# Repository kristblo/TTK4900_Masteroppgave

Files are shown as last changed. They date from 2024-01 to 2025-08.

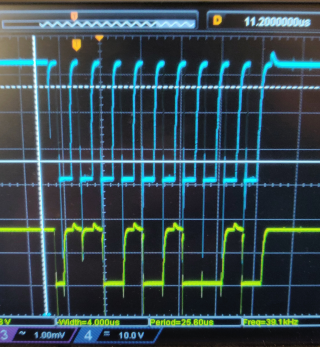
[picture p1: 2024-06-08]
documentation_internal/images/i2c_failure_small.png

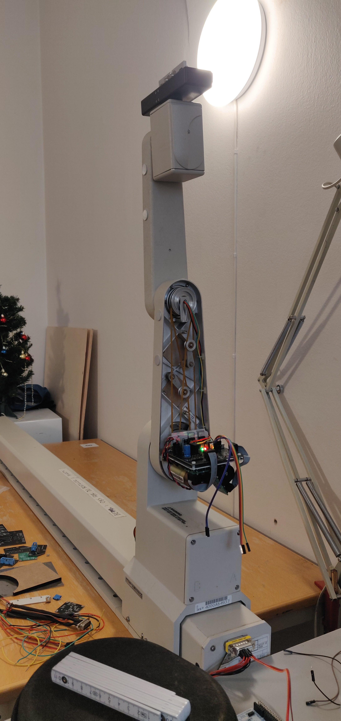
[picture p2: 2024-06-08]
documentation_internal/images/1704_real_arm_calibrated.jpg

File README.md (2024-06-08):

# TTK4900 Masteroppgave

Welcome to the Git repo of the master thesis project of Kristian Blom the spring of 2024, in which a defunct robotic arm from the 1990s was refurbished with new control hardware and software.

The main branch presents the project as it was at the end of the project's implementation, and shall not be altered until final censure has fallen on the project report.

The censure branch presents a curated version of project items deemed relevant to censure. Should the censor(s) find the main branch unnecessarily cluttered, this branch may be of interest.

### Directory: PCBs
Contains KiCad PCB design files.

### Directory: code/ros
Contains all code pertaining to ROS nodes and their configuration.

### Directory: code/stm config official
Contains all code pertaining to arm onboard software modules.

### Directory: documentation external
Contains hardware datasheets, application notes etc. for units used in the project. Most of these are cited as sources in the report.

### Directory: documentation internal
Contains documentation generated for the project.

The file journal.md contains notes taken during development.

A PDF version of the generated code documentation may be found here, in the file "kristian\_blom\_ttk4900\_documentation.pdf".

An HTML version of the generated code documentation may be found here, in the file "kristian\_blom\_ttk4900\_documentation\_html.zip". Its contents may be accessed by downloading and extracting the zip, then accessing "index.html" from a web browser.

Should the configuration of the STM32F303 processor be of interest, beyond what is presented in the thesis, an automatically generated report may be found in "stm\_config\_official.pdf"

Other items in this directory deemed relevant to the censure of the project are presented in the thesis, and may safely be ignored.

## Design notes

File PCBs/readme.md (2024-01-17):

###Folder purpose: PCB designs with Mk1.1 updates implemented, as well as production files such as gerbers

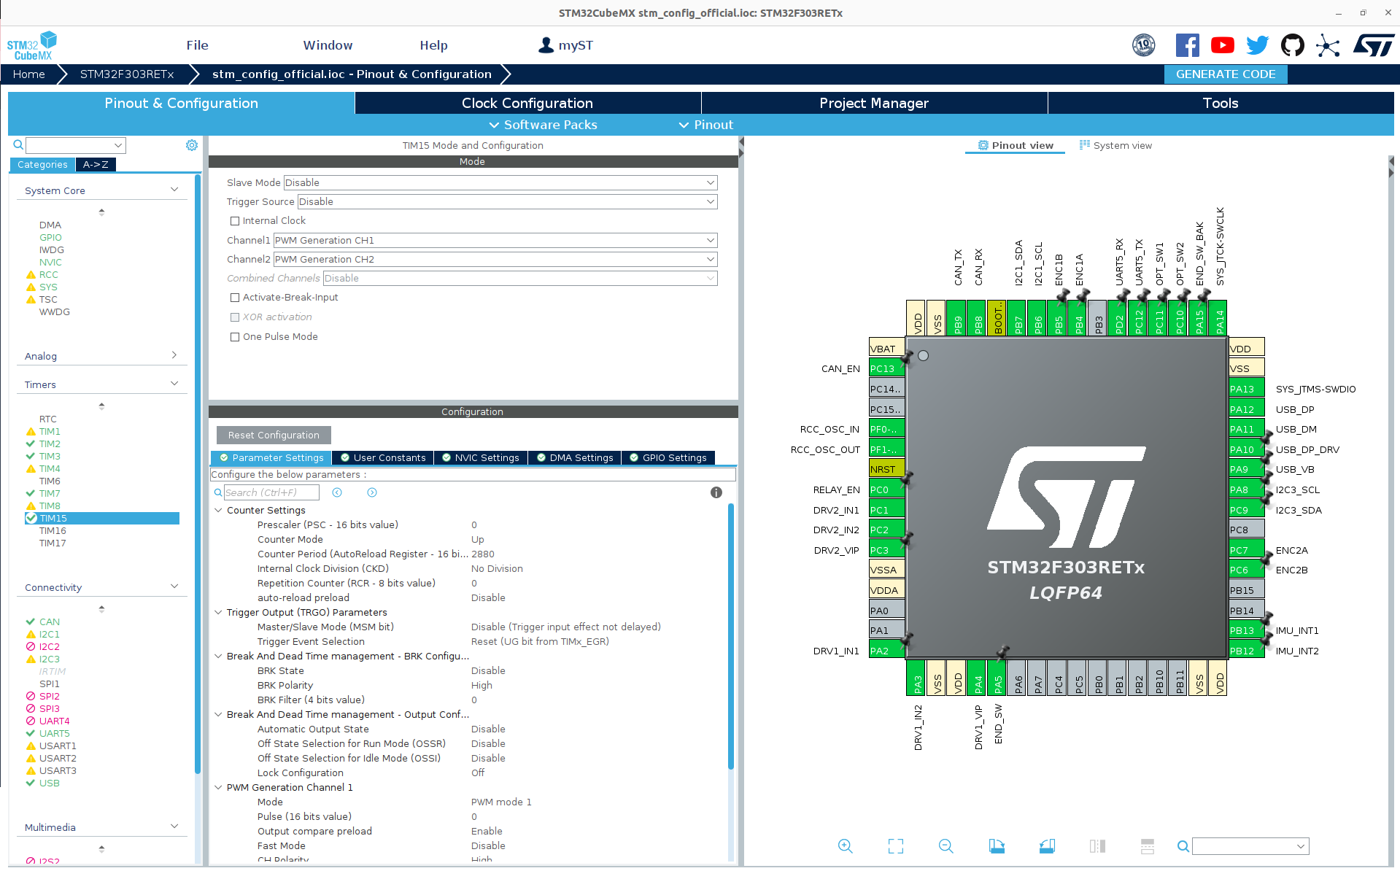
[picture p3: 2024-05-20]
documentation_internal/illustrations/cubemx_pinout_illustration.png

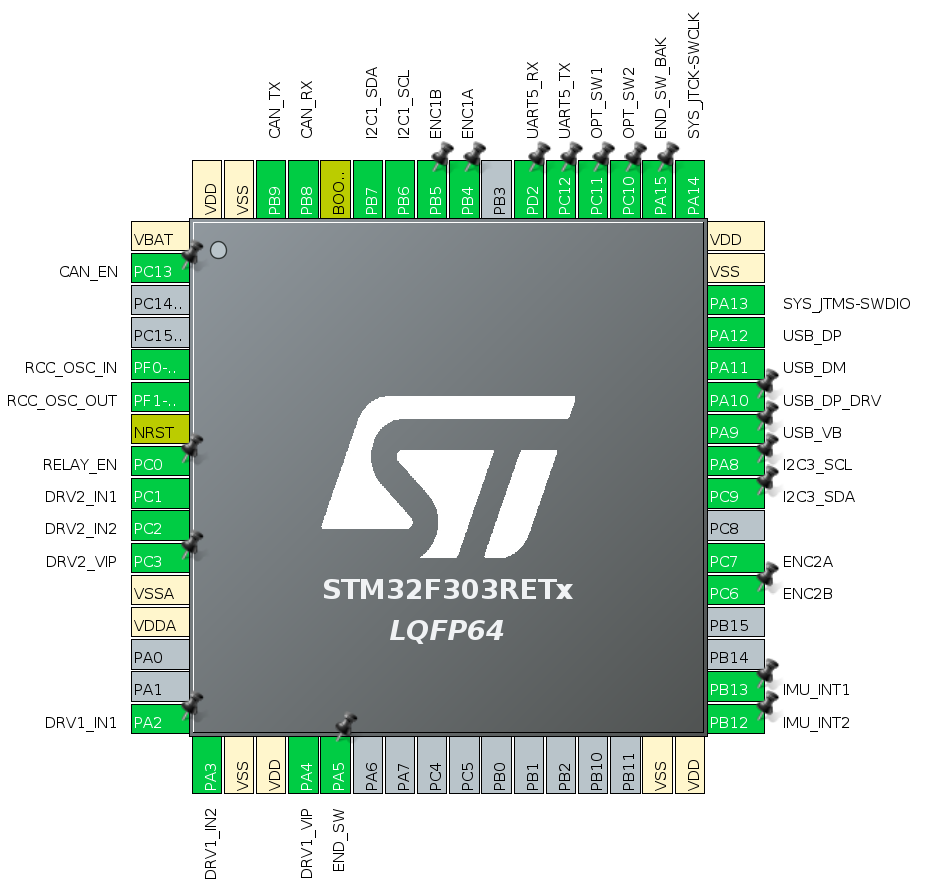
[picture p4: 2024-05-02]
documentation_internal/illustrations/mcu_pinout_illustration.png

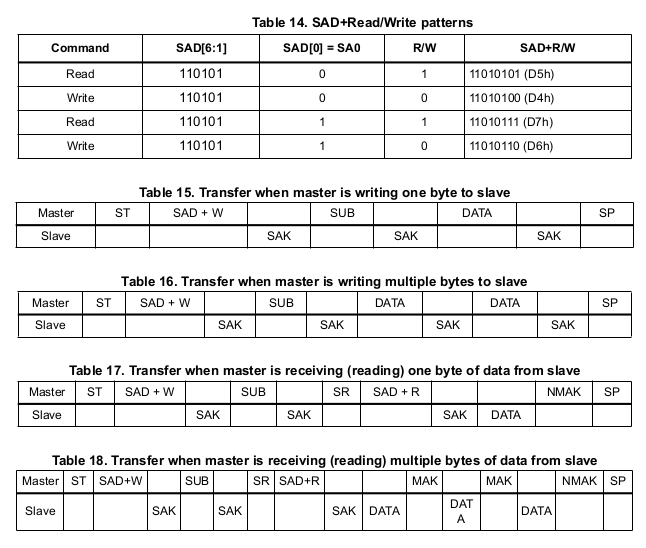
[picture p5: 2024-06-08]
documentation_internal/illustrations/theory/i2c_lsm_ptcl.png

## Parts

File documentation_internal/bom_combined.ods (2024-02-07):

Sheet: All_boards
Type | Footprint | Name | Quantity | OV | Left over | Mouser | Mouser nr
Capacitor | C_0603_1608Metric | 100nF | 37 |  | 0 | 40 | 581-06035C104KAT2A
Capacitor | C_0402_1005Metric | 100nF | 2 |  | 0 | 2 | 581-04025C104KAT4A
Capacitor | C_0603_1608Metric | 10nF | 3 |  | 0 | 3 | 581-06035C103J
Capacitor | CP_Axial_L10.0mm_D4.5mm_P15.00mm_Horizontal | 10uF | 2 |  | 1 | 2 | 594-2222-021-38109
Capacitor | CP_Radial_D5.0mm_P2.00mm | 10uF | 8 |  | 2 | 10 | 667-EEU-FC1H100LH
Capacitor | C_0603_1608Metric | 1uF | 3 |  | 0 | 3 | 581-06035C105KAT2A
Capacitor | C_0603_1608Metric | 20pF | 6 |  | 0 | 6 | 581-06035A200J4T2A
Capacitor | CP_Radial_D10.0mm_P5.00mm | 220uF | 1 |  | 0 | 1 | 591-MAL214651221E3
Capacitor | C_0603_1608Metric | 4.7uF | 3 |  | 0 | 3 | 581-06036D475K
Capacitor | CP_Elec_6.3x7.7 | Hand motor cap 47uF | 6 | 6 | 0 | 0
Capacitor | CP_Radial_D16.0mm_P7.50mm | Motor cap 330uF | 3 |  | 0 | 3 | 667-EEU-FS1H331B
Connector | TerminalBlock_4Ucon_1x04_P3.50mm_Vertical | CAN and Power connector | 3 | 0 | 3 | 0
Connector | PinHeader_2x05_P2.54mm_Vertical | Encoder connector | 4 |  | 0 | 0
Connector | USB_Micro-B_Molex-105017-0001 | Micro USB port | 2 | 2 | 0 | 0
Connector | 70543-0001_MOL | Molex Motor connector | 4 |  | 0 | 4 | 538-70543-0001
Connector | 2-1761603-6_TYC | TE Connectivity 16 pin | 2 |  | 0 | 2 | 571-2-1761603-6
Connector | 1761681-7_TYC | TE Connectivity 20 pin | 2 |  | 0 | 2
Crystal | XTAL_ABL-16_ABR | 16MHz crystal | 3 |  | 0 | 3 | 815-ABL16000MHZB1UT
Diode | D_T-1_P5.08mm_Horizontal | 3.3V Zener | 3 | 3 | 0 | 0
Diode | D_T-1_P5.08mm_Horizontal | IN4005 | 12 | 12 | 0 | 0
IC | CDSC706-0504C_BRN | CDSC706-0504C TVS | 1 |  | 1 | 1 | 611-CDSC706-0504C
IC | SOIC8_DDA_TEX | DRV8251A Motor driver | 6 | 0 | 0 | 13 | 595-DRV8251ADDAR
IC | TO-220-3_Horizontal_TabDown | LM317_TO-220 Voltage reg | 6 | 0 | 4 | 2 | 926-LM317HVT/NOPB
IC | LGA-14L_2P5X3X0P83_STM | LSM6DSM IMU | 3 |  | 2 | 4 | 511-LSM6DSMTR
IC | OPB971N51 | Optical switch | 1 | 0 | 1 | 0
IC | LQFP-64_10x10mm_P0.5mm | STM32F303RET6 MCU | 3 | 0 | 0 | 3 | 511-STM32F303RET6
IC | SOT96-1_SO8_NXP | TJA1057GT/3J CANTrx | 3 | 0 | 1 | 2 | 771-TJA1057GT/3J
IC | SOT-666_STM | USBLC6-2P6 TVS array | 2 | 0 | 0 | 2 | 511-USBLC6-2P6
IC | SOT-23-3 | ZMR330FTA Voltage reg | 1 |  | 0 | 1 | 522-ZMR330FTA
LED | LED_0603_1608Metric | Indicator LED | 11 | 11 | 0 | 0
Potmeter | Potentiometer_Bourns_3006P_Horizontal | 89R1K something | 6 | 6 | 0 | 0
Relay | JV-3S-KT | Motor enable relay | 2 | 0 | 2 | 0
Resistor | R_0402_1005Metric | 10k | 2 |  | 0 | 2 | 791-RMC10K103FTH
Resistor | R_0805_2012Metric | 10k | 9 |  | 0 | 10 | 791-RMC1/10K1002DTP
Resistor | R_0603_1608Metric | 120Ohm | 2 |  | 0 | 3 | 667-ERJ-PA3F1200V
Resistor | R_0805_2012Metric | 1k5 | 7 |  | 0 | 7 | 603-AC0805FR-071K5L
Resistor | R_0603_1608Metric_Pad0.98x0.95mm_HandSolder | 1k5 | 2 |  | 0 | 2 | 603-RC0603FR-071K5L
Resistor | R_0402_1005Metric | 220Ohm | 1 |  | 0 | 2 | 667-ERJ-U2RD2200X
Resistor | R_0805_2012Metric | 240Ohm | 6 |  | 0 | 6 | 667-ERJ-6GEYJ241V
Resistor | R_0603_1608Metric_Pad0.98x0.95mm_HandSolder | 33k | 2 |  | 0 | 3 | 791-RMC1/16K3302FTP
Resistor | R_0805_2012Metric | 340Ohm | 3 |  | 0 | 3 | 667-ERJ-6ENF3400V
Resistor | R_0402_1005Metric | 40k | 31 |  | 0 | 35 | 603-RT0402FRE0740K2L
Resistor | R_0805_2012Metric | 510Ohm RIPROPI | 6 |  | 0 | 6 | 667-ERJ-6ENF5100V
Resistor | R_0603_1608Metric_Pad0.98x0.95mm_HandSolder | 82k | 2 |  | 0 | 3 | 603-AC0603FR-0782KL
Transistor | TO-92 | 2N551 NPN BJT transistor | 2 |  | 0 | 0

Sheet: Bogie
Id | Designator | Footprint | Quantity | Designation | Supplier and ref
1 | OUT1 | 2-1761603-6_TYC | 1 | Conn_02x08_Top_Bottom
2 | ENC1 | PinHeader_2x05_P2.54mm_Vertical | 1 | Conn_02x05_Odd_Even
3 | H2,H1 | MountingHole_3.5mm | 2 | MountingHole
4 | END_SWITCH1 | PinHeader_1x03_P2.54mm_Vertical | 1 | Conn_01x03
5 | MTR1 | 70543-0001_MOL | 1 | Conn_01x02
6 | MAIN1 | 1761681-7_TYC | 1 | Conn_02x10_Top_Bottom

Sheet: Hand
Id | Designator | Footprint | Quantity | Designation | Supplier and ref
1 | C19,C1,C13,C14,C17,C3,C18,C7,C10,C8,C9 | C_0603_1608Metric | 11 | 100nF
2 | D6,D5,D3,D4 | D_T-1_P5.08mm_Horizontal | 4 | IN4005
3 | C4 | C_0603_1608Metric | 1 | 4.7muF
4 | D2 | D_T-1_P5.08mm_Horizontal | 1 | D_Zener
5 | U1 | SOT96-1_SO8_NXP | 1 | TJA1057GT/3J
6 | U3,U4 | TO-220-3_Horizontal_TabDown | 2 | LM317_TO-220
7 | RV2 | Potentiometer_Bourns_3006P_Horizontal | 1 | 0,706k
8 | R6,R8 | R_0805_2012Metric | 2 | 240Ohm
9 | ENC1,ENC2 | PinSocket_1x05_P2.54mm_Vertical | 2 | Conn_01x05
10 | C_MTR6,C_MTR3,C_MTR2,C_MTR5,C_MTR1,C_MTR4 | CP_Elec_6.3x7.7 | 6 | 47muF
11 | C21,C22 | C_0402_1005Metric | 2 | 100nF
12 | R_IPROPI2,R_IPROPI1 | R_0805_2012Metric | 2 | 510Ohm
13 | R13,R_EN1,R11,R12,R7,R5,R4,R14 | R_0402_1005Metric | 8 | 40k
14 | R27,R31 | R_0402_1005Metric | 2 | 10k
15 | C5 | C_0603_1608Metric | 1 | 1muF
16 | D8 | LED_0603_1608Metric | 1 | LED_5V
17 | R10,R9 | R_0805_2012Metric | 2 | 1k5
18 | XTAL1 | XTAL_ABL-16_ABR | 1 | ABL-16.000MHZ-B2
19 | MTR_DRV2,MTR_DRV1 | SOIC8_DDA_TEX | 2 | DRV8251ADDAR
20 | U5 | LGA-14L_2P5X3X0P83_STM | 1 | LSM6DSMTR
21 | BOOT1 | PinHeader_1x02_P2.54mm_Horizontal | 1 | BOOTMODE
22 | D7 | LED_0603_1608Metric | 1 | LED_3V3
23 | JP1,JP2 | PinHeader_1x02_P2.54mm_Horizontal | 2 | Jumper_2_Open
24 | RV1 | Potentiometer_Bourns_3006P_Horizontal | 1 | 0,386k
25 | C11,C12 | C_0603_1608Metric | 2 | 20pF
26 | D1 | LED_0603_1608Metric | 1 | LED
27 | SRL_FLS_URT1 | PinHeader_2x05_P2.54mm_Horizontal | 1 | Conn_02x05_Odd_Even
28 | R3 | R_0805_2012Metric | 1 | 340Ohm
29 | U2 | LQFP-64_10x10mm_P0.5mm | 1 | STM32F303RETx
30 | R1 | R_0805_2012Metric | 1 | 10kOhm
31 | H1,H2 | MountingHole_2.2mm_M2 | 2 | MountingHole
32 | CAN_TRM1 | R_0603_1608Metric | 1 | 120Ohm
33 | J6 | PinHeader_1x02_P2.54mm_Horizontal | 1 | Conn_01x02
34 | PWR_CAN_IMU1,MTR1 | PinHeader_2x04_P2.54mm_Vertical | 2 | Conn_02x04_Odd_Even
35 | CON_A1 | PinHeader_1x03_P2.54mm_Vertical | 1 | Conn_01x03
36 | C16,C15 | CP_Axial_L10.0mm_D4.5mm_P15.00mm_Horizontal | 2 | 10muF
37 | C6 | C_0603_1608Metric | 1 | 10nF
38 | IMU_OPT1 | PinHeader_1x02_P2.54mm_Vertical | 1 | Conn_01x02

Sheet: Hand_B
Id | Designator | Footprint | Quantity | Designation | Supplier and ref
1 | R1 | R_0402_1005Metric | 1 | 220
2 | H2,H1 | MountingHole_2.7mm_M2.5 | 2 | MountingHole
3 | CON_B1 | PinHeader_1x03_P2.54mm_Vertical | 1 | Conn_01x03
4 | OPT1 | OPB971N51 | 1 | ~

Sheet: IMU
Id | Designator | Footprint | Quantity | Designation | Supplier and ref
1 | R1,R2 | R_0805_2012Metric | 2 | 40k
2 | VLT_DBG1 | PinHeader_1x02_P2.54mm_Vertical | 1 | Conn_01x02
3 | OPT_EN1,INT_EN1,INT_SEL1 | PinHeader_1x03_P2.54mm_Vertical | 3 | Jumper_3_Open
4 | R4,R3 | R_0805_2012Metric | 2 | 10k
5 | C1,C2 | C_0603_1608Metric | 2 | 100nF
6 | H2,H3,H1 | MountingHole_3.2mm_M3_DIN965_Pad_TopBottom | 3 | MountingHole_Pad
7 | D1 | LED_0603_1608Metric | 1 | LED
8 | R5 | R_0805_2012Metric | 1 | 1k5
9 | U2 | SOT-23-3 | 1 | ZMR330FTA
10 | U1 | LGA-14L_2P5X3X0P83_STM | 1 | LSM6DSMTR
11 | OPT1 | PinHeader_1x03_P2.54mm_Vertical | 1 | Conn_01x03
12 | I2C_PWR1 | PinHeader_1x06_P2.54mm_Vertical | 1 | Conn_01x06

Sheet: Rail
Id | Designator | Footprint | Quantity | Designation | Supplier and ref
1 | H2,H3,H1 | MountingHole_3.2mm_M3_DIN965_Pad_TopBottom | 3 | MountingHole_Pad
2 | OUT1 | 2-1761603-6_TYC | 1 | Conn_02x08_Top_Bottom
3 | DSUB1 | PinHeader_2x07_P2.54mm_Vertical | 1 | Conn_02x07_Odd_Even
4 | CR1 | CDSC706-0504C_BRN | 1 | CDSC706-0504C
5 | D1 | LED_0603_1608Metric | 1 | LED

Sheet: Shoulder
Id | Designator | Footprint | Quantity | Designation | Supplier and ref
1 | MTR2,MTR1 | 70543-0001_MOL | 2 | 705430001
2 | D2,D3,D1,D4 | D_T-1_P5.08mm_Horizontal | 4 | IN4005
3 | C_MTR1 | CP_Radial_D16.0mm_P7.50mm | 1 | 330muF
4 | R21,R13,R14,R20,R15,R16,R19,R17,R12,R18 | R_0402_1005Metric | 10 | 40kOhm
5 | ENC1,ENC2 | PinHeader_2x05_P2.54mm_Vertical | 2 | Conn_02x05_Odd_Even
6 | H2,H4,H1,H3 | MountingHole_3.2mm_M3 | 4 | MountingHole
7 | JP2,JP1 | PinHeader_1x02_P2.54mm_Vertical | 2 | Jumper_2_Open
8 | U4,U5 | TO-220-3_Vertical | 2 | LM317_TO-220
9 | RV2 | Potentiometer_Bourns_3006P_Horizontal | 1 | 0,706k
10 | C5,C8,C9,C15,C3,C4,C2,C1,C14,C20,C19,C21,C22 | C_0603_1608Metric | 13 | 100nF
11 | CAN_TRM1 | R_0603_1608Metric | 1 | 120Ohm
12 | C12,C13,C10,C11 | CP_Radial_D5.0mm_P2.00mm | 4 | 10muF
13 | J1 | USB_Micro-B_Molex-105017-0001 | 1 | USB_B_Micro
14 | C16 | C_0603_1608Metric | 1 | 4.7muF
15 | Q1_RLY_CTRL1 | TO-92 | 1 | Q_NIGBT_CGE
16 | R1_IPROPI1,R2_IPROPI1 | R_0805_2012Metric | 2 | 510Ohm
17 | D6 | LED_0603_1608Metric | 1 | LED_5V
18 | MTR_DRV1,MTR_DRV2 | SOIC8_DDA_TEX | 2 | DRV8251ADDAR
19 | R2 | R_0603_1608Metric_Pad0.98x0.95mm_HandSolder | 1 | 33k
20 | R5,R4 | R_0805_2012Metric | 2 | 10k
21 | JV-3S-KT1 | JV-3S-KT | 1 | RELAY
22 | D8 | D_T-1_P5.08mm_Horizontal | 1 | D_Zener
23 | C17 | C_0603_1608Metric | 1 | 1muF
24 | U2 | LGA-14L_2P5X3X0P83_STM | 1 | LSM6DSMTR
25 | D5 | LED_0603_1608Metric | 1 | LED_3V3
26 | U3 | SOT96-1_SO8_NXP | 1 | TJA1057GT/3J
27 | J3,RLY_CTL_DBG1 | PinHeader_1x03_P2.54mm_Vertical | 2 | Conn_01x03
28 | SW1 | SW_Push_1P1T_NO_CK_KSC6xxJ | 1 | RESET
29 | XTAL1 | XTAL_ABL-16_ABR | 1 | ABL-16.000MHZ-B2
30 | PWR_CAN_IN1,PWR_CAN_OUT1 | TerminalBlock_4Ucon_1x04_P3.50mm_Vertical | 2 | Conn_01x04
31 | U1 | LQFP-64_10x10mm_P0.5mm | 1 | STM32F303RETx
32 | UART1 | PinHeader_1x02_P2.54mm_Vertical | 1 | Conn_01x02
33 | SRL_FLASH1 | PinHeader_1x05_P2.54mm_Vertical | 1 | Conn_01x05
34 | R9,R8 | R_0805_2012Metric | 2 | 240Ohm
35 | R3 | R_0603_1608Metric_Pad0.98x0.95mm_HandSolder | 1 | 1k5
36 | C7,C6 | C_0603_1608Metric | 2 | 20pF
37 | BOOT1 | PinHeader_1x02_P2.54mm_Vertical | 1 | BOOTMODE
38 | C_MTR2 | CP_Radial_D10.0mm_P5.00mm | 1 | 220muF
39 | RV1 | Potentiometer_Bourns_3006P_Horizontal | 1 | 0,386k
40 | R11,R10 | R_0805_2012Metric | 2 | 1k5
41 | J2 | PinHeader_1x07_P2.54mm_Vertical | 1 | Conn_01x07
42 | R7 | R_0805_2012Metric | 1 | 10kOhm
43 | CR1 | SOT-666_STM | 1 | USBLC6-2P6
44 | R6 | R_0805_2012Metric | 1 | 340Ohm
45 | R1 | R_0603_1608Metric_Pad0.98x0.95mm_HandSolder | 1 | 82k
46 | D7 | LED_0603_1608Metric | 1 | LED
47 | C18 | C_0603_1608Metric | 1 | 10nF

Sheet: Torso
Id | Designator | Footprint | Quantity | Designation | Supplier and ref
1 | C11,C12 | C_0603_1608Metric | 2 | 20pF
2 | H5,H3,H4 | MountingHole_5.3mm_M5 | 3 | MountingHole
3 | C2,C13,C4,C10,C1,C3,C9,C19,C20,C18,C17 | C_0603_1608Metric | 11 | 100nF
4 | BOOT1 | PinHeader_1x02_P2.54mm_Vertical | 1 | BOOTMODE
5 | R1,R2 | R_0805_2012Metric | 2 | 240Ohm
6 | R20,R19,R12,R16,R14,R15,R18,R10,R13,R17,R11 | R_0402_1005Metric | 11 | 40kOhm
7 | C15 | C_0603_1608Metric | 1 | 1muF
8 | U1 | SOT96-1_SO8_NXP | 1 | TJA1057GT/3J
9 | R3,R4 | R_0805_2012Metric | 2 | 1k5
10 | C_MTR2,C_MTR1 | CP_Radial_D16.0mm_P7.50mm | 2 | 330uF
11 | R5 | R_0603_1608Metric_Pad0.98x0.95mm_HandSolder | 1 | 82k
12 | D4,D2,D1,D3 | D_T-1_P5.08mm_Horizontal | 4 | IN4005
13 | C5,C7,C8,C6 | CP_Radial_D5.0mm_P2.00mm | 4 | 10muF
14 | UART1 | PinHeader_1x02_P2.54mm_Vertical | 1 | Conn_01x02
15 | JV-3S-KT1 | JV-3S-KT | 1 | RELAY
16 | CAN_TRM1 | R_0603_1608Metric | 1 | 120Ohm
17 | R_IPROPI2,R_IPROPI1 | R_0805_2012Metric | 2 | 510Ohm
18 | SRL_FLASH1 | PinHeader_1x05_P2.54mm_Vertical | 1 | Conn_01x05
19 | D7 | LED_0603_1608Metric | 1 | LED
20 | U3,U2 | TO-220-3_Horizontal_TabDown | 2 | LM317_TO-220
21 | D8 | D_T-1_P5.08mm_Horizontal | 1 | D_Zener
22 | RV2 | Potentiometer_Bourns_3006P_Horizontal | 1 | 0,706k
23 | LO_V_DBG1,RLY_CTL_DBG1 | PinHeader_1x03_P2.54mm_Vertical | 2 | Conn_01x03
24 | SW1 | SW_Push_1P1T_NO_CK_KSC6xxJ | 1 | RESET
25 | Q1_RLY_CTRL1 | TO-92 | 1 | Q_NIGBT_CGE
26 | H2,H1 | MountingHole_3.5mm | 2 | MountingHole
27 | CR1 | SOT-666_STM | 1 | USBLC6-2P6
28 | MTR_DRV2,MTR_DRV1 | SOIC8_DDA_TEX | 2 | DRV8251ADDAR
29 | D6 | LED_0603_1608Metric | 1 | LED_5V
30 | J3 | USB_Micro-B_Molex-105017-0001 | 1 | USB_B_Micro
31 | MAIN1 | 1761681-7_TYC | 1 | Conn_02x10_Top_Bottom
32 | U4 | LQFP-64_10x10mm_P0.5mm | 1 | STM32F303RETx
33 | RV1 | Potentiometer_Bourns_3006P_Horizontal | 1 | 0,386k
34 | R6 | R_0603_1608Metric_Pad0.98x0.95mm_HandSolder | 1 | 1k5
35 | JP2,JP1 | PinHeader_1x02_P2.54mm_Vertical | 2 | Jumper_2_Open
36 | C14 | C_0603_1608Metric | 1 | 4.7muF
37 | R8 | R_0805_2012Metric | 1 | 10kOhm
38 | R9 | R_0805_2012Metric | 1 | 340Ohm
39 | XTAL1 | XTAL_ABL-16_ABR | 1 | ABL-16.000MHZ-B2
40 | MTR_ASY_DBG1 | PinHeader_1x07_P2.54mm_Vertical | 1 | Conn_01x07
41 | PWR_CAN_OUT1 | TerminalBlock_4Ucon_1x04_P3.50mm_Vertical | 1 | Conn_01x04
42 | MTR2 | 70543-0001_MOL | 1 | 705430001
43 | ENC1 | PinHeader_2x05_P2.54mm_Vertical | 1 | Conn_02x05_Odd_Even
44 | R7 | R_0603_1608Metric_Pad0.98x0.95mm_HandSolder | 1 | 33k
45 | D5 | LED_0603_1608Metric | 1 | LED_3V3
46 | C16 | C_0603_1608Metric | 1 | 10nF

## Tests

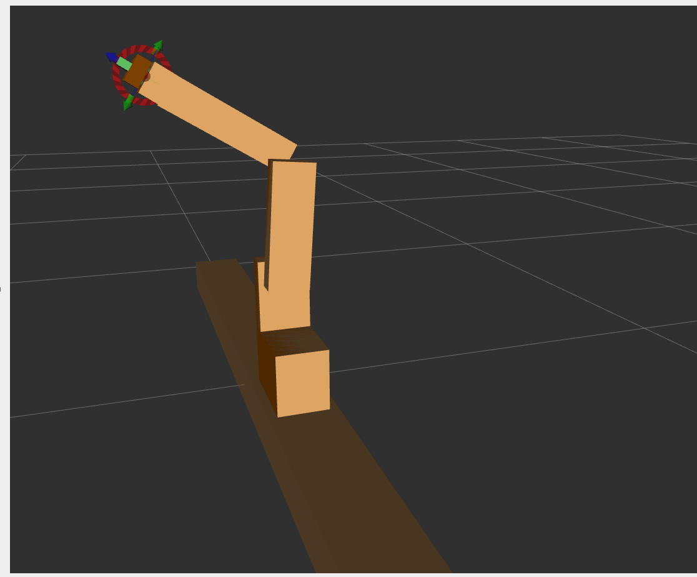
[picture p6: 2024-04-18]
documentation_internal/images/1704_arm_position_test0.png

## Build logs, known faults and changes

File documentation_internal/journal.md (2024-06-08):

##Journal
Notes and findings made during the semester. It's easier to collect everything in one file than to have an assortment of "misc" files. Replaces the journaling style commit messages from the specialisation project.
Date format: DDMMYY

###160124
Read the USB application note AN4879. It recommends two specific components for ESD protection, both of which are availabe on Mouser. Should probably implement that. Also, a transistor is probably not necessary to drive the DP line. The figure text on fig 5 implies that the GPIO pin just needs to be taken out of reset/floating when VBUS is detected.

###170124
Looks like all the MCU changes are implementable without issues. Taking care to move optical switches and end switch detector to FT pins. Found that the 2N551 NPN BJT transistor can operate the relay. Found that the end switch and wrist optocoupler work on 5V, but measure only 2.7V on the output. Should be well over the 5VT VIH threshold. Breadboarded a circuit for the OPB sensor, works. The sensor (i.e. LED+resistor) was placed between Vcc and OUT. Activates when aperture is abstructed to measure approx 3V. Measured -0.6V before activation, not acceptable. Measured [-0.150,0.050]V before avtivation after removing the LED+resistor, acceptable. Also 5V on activation.

Radical idea: Put the shoulder IMU on the shoulder. No need to have an extra board in the upper arm, it saves on wiring and the assembly can be reused in the hand.

###180124
Installed the recommended USBLC6 ESD protection from AN4879. Completed the shoulder board with few notes. Rotated the MCU 90deg ccw relative to MK1 because it fit better with the motor drivers. Not a huge impact overall, if anything it made the whole layout simpler/easier to look at. Had some trouble with the encoder connector footprints not matching the symbol's pad enumeration, switched to odd/even compared to ccw in MK1. Electrically identical ofc.

Voltage tuning resistors are connected with the other leg compared to MK1. Don't remember reassigning them in that design, but it shouldn't matter. Tested on OV.

Consider setting up I2C headers such that it can be used instead of CAN if that really doesn't work. For the hand, that probably means committing to having both IMUs on the same bus.

###190124
The added hardware complexity of being able to switch between CAN and I2C is not worth it. Would need extra jumpers (or even DIP-switches) to enable or disable all relevant pins, and introducing two IMUs on one I2C w/o testing is asking for trouble. The TTK8 breadboard tests showed that the CAN hardware is probably correct.

Changed end switch to PA5 to better fit torso layout.
Decided against finding a new TVS. I'm not sure I'd find one actually able to protect my 48V lines w/o frying the other lines. All my data lines are protected with the old one, CDSC706, and the 48V lines are to some extent protected by diodes near all the voltage regulators.

###240124
Found dc-buck ZMR330FTA for use on the IMU board. This saves one wire (or 14%!) from the interface. Still need gnd, 5v, opt, int, sda, scl, but a simple test with jumper wires indicates that this will be OK. I'm increasingly unsure of how I'm supposed to route wires inside the hand, however.

For wiring: try to rework the board outline to make space for them. The new IMU header solution was to remove the 2x2 interrupt header/jumper in favor of a 1x2 header for IMU and OPT interrupts, for a marginally smaller footprint than the previous design. The IMU board itself can have a pulldown and ENABLE jumper to pull all unused low -- plenty of space there.

###250124
Further investigation of the hand board shows that I can expand it by 2mm right and fit all the connectors on vertical headers, similar to the original ribbon between A and B. Also made a similar tab to move the OPT header ~2.5mm up.

Switched I2C ports for the IMUs such that the on-board IMU gets port 3. Fits better with the layout.

Realised the larger damping caps on the MCU were connected between the zener and its LED instead of 3V3. Make sure that's not the case on other designs!

Finished traces and silk on hand. IMPORTANT: Find a footprint for "Flush mount socket" on the encoder connectors before sending to JLC.

###260124
Decided to reuse the old sockets instead of trying to find a replacement model. Don't know enough about the type of connector etc. Made a new footprint by increasing the hole diameter of a standard 2.54mm header from 1.0mm to 1.5mm, and the pad diameter to 2.2mm to comply with JLC's requirement of 0.3mm minimum annular ring. Shifted both footprints 0.3mm left on the PCB, looked like that might be a better fit. Motivated by the observation that the sockets were not placed on the centerline between the square holes.

Created Hand B as a separate Kicad project for the optical sensor in order to comply with the goal of avoiding multiboard production. Two layers, all standard settings.

###020224
Discovered that fitting all the wires inside the lower arm will be a challenge, at least w/o spaghetti wires. They don't really fit without interfering with the actuation belts. Not insurmountable, but probaby won't be able to put the covers back on without some minor modding.

###030224
Ordered the wrong CAN transcievers. Got GT instead of BT, which don't have the variable VIO pin. Will salvage the BTs from Mk1. The TRx on the test bench unit which iirc was attached to the test bench MCU is also GT, which may explain the negative result from the CAN tests.

Opened the rail board to look at the DSUB pinout, found that the 48V fill zone is unfilled due to lower priority than the surrounding zone. Will need to be scraped and soldered on arrival!

###180224
Solved the CAN transceiver problem by salvaging from the old units. Strongly regretting not ordering a full complement of voltage regulators and relays. The relays were a pain in the ass to remove, and the voltage regs now have 40 week lead time if I ever need new ones. Still got two left from the old hand. Also forgot to order the 20 pins, so that's a delay.

Something went wrong during the soldering of the shoulder, I think, as there now is a connection between the voltage regulators making them move in tandem when I tune them. Solution: this is why we isolate our heat sinks with silpads <3

All three units tuned for voltage.

Set the relays to toggle on and off with one second intervals, workSet the relays to toggle on and off with one second intervals, works.

###210224
Discovered that I've flipped the resistors of the USB voltage divider. Switched them, still no detection. I realise that I probably need to activate the DP driver somehow, but I haven't found the right place to do it -- probably some callback function.

UART works with the devkit, just had to remove two solder bridges. Makes USB less appealing.

I2C does not seem to work, might be hardware. The waveform looks very unstable, unlike previously. Possibly need a different resistor value, or reworking the solder as the IMU board connector really is full of glue. On the other hand, the hand on-board IMU does not seem to work either. Next up: recreate the test bench IMU setup and hook it up to the hand. Find a 5V-3V3 buck somewhere.

###220224
Breadboard IMU works (got whoami) from hand, shoulder IMU also works. This means that the schematic is correct, and that the configuration of both I2C1 and I2C3 is viable. Poor soldering is improbable, as two IMU boards (soldered a second one) and the hand are not all likely to fail. Next up: a thorough review of the PCB layouts to look for possible fuckery, such as bad fill zones.

###230224
Found an Adafruit replacement for the IMUs, MMA8451 breakout. 5V supply, interrupt output etc. Will bite the bullet and order two before I go home if I can't find the solution to the I2C problem.

Beeped all pads on the hand and IMU boards, all clear. Found one difference between shoulder (functional) and hand: C22 on the hand is connected to pin 5 VDDIO on hand, but not on the shoulder. Hand is technically correct, but shoulder is functional, so... Ditto for C1 on the IMU. Removing C1 did not change anything.

Tested with a new IMU on the IMU board, same result. Got one clue, however: when the breadboard unit's interrupts are left floating, it too becomes unable to respond. Unfortunately, setting the relevant GPIO pins high on the hand did not solve anything. Looks like it's going to be Adafruit. Got screengrabs of the bad IMU board test and the successful breadboard test.

Z axis of shoulder also seems to be dead, but not X axis. Might it actually be that this is not my fault, and I'm just dealing with a bad batch? I'll never know for sure. The shoulder Z axis would have been optimal, but X will work too!

Motor drivers work as expected. Turns out the CCRs are unique to each channel, so the DT function currently always writes to CCR1, 2 and 3. Should probably be part of a motor driver struct in the real project.

###240224
Got CAN working. Should probably cite the youtube video? After watching the first video I simply switched to normal mode, and flashed torso and shoulder with corresponding sender IDs and filters. Now I'm even more certain that my trouble with CAN before Christmas was due to having ordered the wrong transciever.

Will need to read RM0316 chapters 8 (Peripheral interconnect matrix), 13 (DMA), 15 (ADC), 30 (UART) and 31 (bxCAN) as research for the architechture. A key point will be to offload the CPUs as much as possible, in particular CAN/UART should as far as possible avoid the CPU. Unfortunately, UART5 is not compatible with "continuous communication using DMA". Figures!

Discovered that the main connector on bogie is still wrong, most likely a 180 degree rotation around the Z axis. Other than that, all units seem to fit acceptably well. Measures will need to be taken to properly isolate the hand, such as filing down all solder points and taping conductive contact surfaces in the chassis.

###260224
Main connector was 180 degrees around the X axis, i.e. pins 1 and 11 switched places with 10 and 20, respectively. Bogie Mk1.2 changes: Edited bogie schematic by "flipping the symbol from top to bottom", and leaving everything else. Retraced PCB accordingly. Changed mount points from 3.5mm to 3.7mm. Updated silk of main connector to match new layout, version to 1.2. Now feel relatively confident that it will work.

As the rail board was missing a fill zone, I figure I might as well reorder that too. Rail Mk1.2 changes: Updated version silk, fixed fill zones and some additional stitching.

Decided to check Hand B as well, and it is faulted. Will need to debug that before ordering the next batch.

###280224
Didn't explicitly find the source of the Hand B fault, but footprint pins 1 and 2 of the optical switched were swapped. Fixed and sent Hand B, Rail and Bogie Mk1.2 to production. Also ordered full complement of parts from Mouser, don't want to spend the time trying to dismantle Mk1.1 for parts.

###060324
Bogie OK. Optical sensor works, but the MCU will always measure between OUT and GND, not Vcc and OUT as the design is made for. Solution: Put resistors between Vcc and OUT, and OUT and GND of equal size (or possibly slightly higher between OUT and GND). During normal operation, the output pin will measure 2.5V (or higher) which is sufficient for FT VIH (1.85V). When the sensor is triggered, the lower half will be shorted to ground, making the OUT voltage 0V. Configure interrupt for falling edge, and Bob's your uncle. Tested on breadboard, not irl. Soldered resistors on Hand B.

The connection from torso to rail seems OK, except the rows on the silk of the rail card are switched horisontally as the signals reach the actual DSUB connector.

Before properly getting to work, I will shorten the hand A/B connector, remove the IMU board wires, and fasten the torso power regs with silpads and nylon bolts.

###070324
Something wrong with the PWM generation, need to look up the counter period calculation stuff.

###080324
The counter period in the timer init is what actually decides the pwm fqc, CTR_PRD needs to mirror that. The higher the frequency, the lower the resolution -> Can probably survive a lower frequency than 25kHz to get more precise control than 1/2880th. This may be part of the motor characterisation and can be solved analytically, but experimentally 10kHz (7200) is also okay.

Got a funny bug trying to use strcpy to parse input strings. My parser sets all indeces in a holding buffer to 0 upon registering an enter key press. In any other case, it increases the pointer to the holding buffer and then inserts the character. This makes the first entry of the buffer always 0, which strcpy (and sprintf) interprets as EOF. Solution: insert character, then increase pointer.

Various bugs later, I have positioning over UART. Need to figure out how to safely translate full rotational range and count, i.e. overflow from the encoders. Important note: The encoder timers must be activated to function. Also, positive paadrag means the GoFWD should be called.

Will probably need to get interrupts if multiple motors are to be controlled outside of the main loop.

Forwards and backwards is not the same for all motors.

Not registering input from the bogie encoder. Could be HW.

###090324
The encoder bug was indeed HW, the 5V pin on the torso connector was not properly soldered. Neither was one of the ground pins on the bogie, but I don't think that was related.

CAN is not working. Open a new branch with a clean slate and follow the youtube video again.

###120324
Got CAN working again, as well as set up a structure for the project.
CAN: Followed the instructions carefully, and it worked. Then I replicated the setup in the main branch, and it did not work. For some reason, the rx interrupt callback wouldn't trigger. Solution: delete the generated can.c file from main, and check it back out from can\_verification onto main. Then it worked again.
NOTE: restarted cubemx, the generated code. CAN did not break, so I assume this means it is safe to continue.

Structure: my own \_driver files are in a separate folder. Modifying the Makefile between generation in cubeMx is safe. Also discovered a way to make default variables using structs and variable define statements, see can\_driver.c and can\_driver.h.

Got more trouble as soon as I started to send data. Can't find the correct data type for IDE and RTR, which corrupts the whole frame apparently. Fair enough, wasn't really interested in them anyway. They're hardcoded to their default values of STD and DATA now. Instead, I added an argument for mailbox, which I might actually end up needing. Also added the shoulder back into the loop, works.

###130324
Set up a system of function pointers to call on string commands, but having trouble passing data into them. Will probably need use pointers.

###140324
Got a ways further on the string parsing system, but passing information between entities remains a problem. I thought I'd solved motor control by having a static struct writeable by functions in the motor driver header, but apparently even changes to that fall out of scope once the interrupt handler is done (haven't been able to confirm that entirely). Consider running an "update motor power" function in main while, with the function definition in the motor driver.

###150324
Having serious trouble understanding how to use static variables for motor control, i.e. where their scope ends. The solution seems to be to make the static variable in the .c file, and local functions to use it via pointer. Then, to provide an interface outside of the .c file, make interface functions which call the driver functions without passing the static variable directly.
Ex:
motor\_driver\_set\_power(&static\_var, power) is called by
motor\_interface\_set\_power(power),
where the latter SHOULD work from any file which includes the relevant .h file.

All in the name of clean interfaces and memory protection. Additionally, I had a good time debugging the fact that writing to uart doesn't always work in main unless a delay of at least 20ms is inserted. Not sure why, but I suspect it's related to interrupt routines somehow.

Implemented encoder counter which doesn't entirely shit itself after just 16 bits. Interprets a difference in measurement of more than 1000 as a jump in the encoder register, which means it's entirely reliant on being able to measure this faster than every 2 rotations of the motor. Probably safe for low speeds, possibly entirely unsafe for higher.

###160324
Description of module function names:
module\_driver\_get\_thing(): Return a value relevant to the module, effectively only useable inside the module if using static var.
module\_driver\_set\_thing(thingVal): Set the same value, also only for internal useage.
module\_driver\_update\_thing(): Use a heuristic to automatically update the value, may or may not make use of the setter function.
module\_interface\_get\_thing(): Call the corresponding driver function. This function is avaiable outside the module, and is the intended way to interact with a module.

That is: driver functions are for module internal usage and communicate directly with hardware. Interface functions are for external usage. Why? Want to minimise the use of global variables, but also need somewhere to store data. Module internal variables (such as the motor controller descriptor) should be static, which prevents their useage outside of their compilation module (data encapsulation). This necessitates a set of interface functions not directly using the static variables.

Pinch polarity is opposite of everything else, gotta rewrite some stuff.

Rail has a movement range of approximately 145000 encoder counts.
Shoulder range approx 70000 counts.

The CAN driver function names need to be rewritten to conform to the above naming scheme. Started writing the CAN rx handler, and there needs to be multiple message handlers, possibly make another set of function pointers. Immediately, having the unique motor ids internal to the structs and thus changing with each build seems cumbersome. Arguably rewrite the current to do an ACTIVE UNIT check and select manually, as the number of motors is not subject to change. Encoding string input to the can messsages is not difficult, however.

###170324
Got CAN control working! Also fixed some of the function names. I think I should probably make the rx handler more slim, e.g. by storing data in one static uint8 array per type of command rather than parsing it in the interrupt handler directly. Could set a flag which is polled by the main function to look for new messages. However, the MCU runs at 72MHz, the CAN bus at 500kHz, and the UART at 115kHz. I ultimately don't think it'll be a problem that the interrupt handler takes too long, as long as any "real" computation happens in the main function. Besides, what is the point of the CAN FIFO if not to store unread messages?

Next priority is to make an accelerometer driver. It absolutely has to accommodate the shoulder unit, and it should be adaptable for both I2C handles on both hand and shoulder. A set of CAN and string commands should let a motor be controlled such that the accelerometer reaches a certain G measurement.

Thoughts on zero calibration, state estimation: Rail has the end switch, and I think the encoder counter is reliable enough that a range of 145000 clicks is always safe. Shoulder has accelerometer, all good. Twist has the optical sensor, and can probably rely on encoder. Pinch can be gently run until it stops in either end during a calibration phase, then rely on encoder, ditto for wrist after twist has been secured 90 deg on the joint. Elbow may be run until stop while elbow points straight up, but that is inelegant.

As a last-ditch, desperate attempt at making the Adafruits work, I could try to make a voltage divider to get the 5V down to 3.3V, which I suppose is really the "logic level" of my STMs.

###190324
Shoulder accelerometer: acceleration works for x and y axes. X is irrelevant (always 0), Y will be 0 when joint point upwards, plus/minus 1 when horizontal. Needs an offset of approximately 2500, probably due to slighty skewed installation. Rotation rate works for all axes, but only X is relevant.

Wrote a motor controller.h, it almost completely shoulder centric. The loop now works, but is completely unstable. Will need to implement something so that the motor doesn't spaz out, such as setting isMoving to 0 or simply lowering the gain even more.

###200324
Struggling to make the torso to shoulder update loop work. I seems almost random whether or not the function call stack actually results in a correct read or not, will need some debugging.

Got an angle measurement thingy:
Shoulder has -332 encoder clicks per degree forward (CCW when sitting at the desk)
Elbow: 703 clicks/deg forward CW
Wrist: 300 clicks/deg forward CCW
Twist: 155 clicks/deg forward CCW viewed from the front
Pinch: 500 clicks/mm forward opening
Rail: 95 clicks/mm forward towards the end switch

Spent a couple hours debugging a compiler error that only solved by rebooting the computer ffs. Seemed like the CAN rx interrupt read a message twice, returning trash. Wrote an algorithm for controlling the shoulder on paper. FIND OUT: does the accelerometer do the sine conversion to angle for me, or will I need trig?

###210324
For some reason, the CAN rx interrupt seems to trigger twice when receiving a message from the shoulder/accelerometer, and it contains only trash on the second reading. The second interrupt is handled before the control loop finishes, so all accelerometer readings via CAN are trash as far as the control loop is concerned. The solution is to only handle the message when newmsg is 0. Feels very hacky. The printing of debug messages, understandably, seems to alter behaviour in a very hard to predict manner. I really wish the debugger worked. 
Edit: The messages now come in random order, effectively making it impossible to incorporate accelerometer data. Tried manually clearing the CAN_IT_RX_FIFO0_MSG_PENDING flag as well, but no luck.

Decided to rewrite the can driver such that the interrupts almost don't do anything, and a poller/handler in the main does most of the work. Made two lists of 8 functions, one for rx handling and one for tx handling. The idea is that each function corresponds to a mailbox, defined as a struct of a newmsg flag and a data container, and represents an action. I.e. breaking up the large handlers from earlier. Things look okay on the transmit side, but rx must be implemented. The first byte in a CAN message now represents the mailbox and corresponding handler functions, so rx must be rewritten so that they don't contain M or A. There probably should be a global list somewhere so that I don't need to remember which mailbox/function pair is dedicated to which functions, but then again it's an embedded system.

When the CAN rewrite is done, I should do a VERY SELECTIVE merge with main. Don't want the accelerometer loop disturbing things, but also don't want to lose the math stuff as it's still relevant for encoder setpoints. Next goal should be to write controllers for each joint, like with the shoulder/accelerometer loop, just without CAN.

###220324
Rewrote the CAN driver. ID is structured with three fields, accelerometer, motor and command. Accelerometer is ID9..8, motor ID7..5, and command ID4..0. Set up another filter bank so that the accelerometer field is DC for motor commands and vice versa. Main loop runs two loops, one for handling each of tx and rx. Rx has a set of action functions associated with it, and an enum to keep track of valid commands. The HAL_rx now only pushes the message into an array of rx messages, which the main loop responds to. As the rx and tx mailboxes are both of equal length, some will probably not be used: the message type decides which mailbox is used, and message types are mostly explicitly either rx or tx. However, we're not short on space and this seems like a safe structure. I've ditched the set of accelerometer commands for now, but may reimplement. Also added doxygen to the driver files, seems to look good! Updated from the command palette, be sure to have the right file open/selected before running. Had to enable basically every 'EXTRACT_' flag to make it realise I actually want every function.

###230324
Changed the CAN config filter names and bank numbers to be less youtubey, including giving the configs unique names on the off chance that reusing them is bad. Making one last attempt at getting stable accelerometer readings, if for no other reason than having a proof of concept.

Got accelerometer readings back, works when only trying to read one value. Will test a bit more.

Otherwise: Got joint control back up with a primitive PI controller, can now set rads/mm setpoints. Set Ki to 0 for most joints as the friction in the system makes it a bit unstable -- either spends too long stabilizing or overshoots heavily. Got more accurate estimates for the resolution of all joints, works quite well. Still working on low speeds ofc, but the encoder counter seems to keep track without issue.

##240324
Set up a timer interrupt on approx 344Hz on TIM2. Idea: based on CAN bus rates etc, accelerometer and motor pos should not be polled more frequently than 350Hz. The interrupt sets to flags, defined in the joint controller module, declaring that enough time has passed since last poll that a new poll is probably safe. This is to avoid bus contention. This may be simpler than trying to find a heuristic for when to measure acceleration in the control loop, and will probably also be helpful for ROS integration: The software can then poll for position and speed in the control loop, with a well-defined (ish) time step.

Good day for architecture! Set up a new set of CAN commands, get axis. Sends a request for rotation and acceleration data for the given axis. Acceleration works well, rotation may need some debugging for whatever reason. Proof of concept in the main loop. One IMPORTANT drawback is that the polling mechanism will always favor messages early in the queue, need to figure out some sort of priority or just think harder on whether it's really a problem. Before merge: Integrate accelerometer readings into the shoulder control loop. Then get to work on ADCs, and hopefully start work on ROS after that.

###250324
Decided to skip right on to ADC driver. Needs a bit more testing, but the main ffeature of turning the relays off above a certain threshold seems to work. The trick was to configure them for continuous mode, that way they'll just keep going after start.

Consider rewriting interface functions in joint control (and others?) to use the structs directly via the struct arrays instead of driver functions. Can get rid of a lot of unnecessary and confusing code that way. And maybe strip some of the joint interface functions? See how many are actually needed after accelerometer integration.

Erlend brought up an interesting point re I2C: could be a polling issue. If the data is sampled just as an edge is rising/falling, the data could be trash, or work spuriously -- which is what I'm seeing. CubeMX doesn't let me change edge polling, and I think I2C has clock and data offset by 90 degrees anyway, but I should investigate the rise/fall time parameters. IMU datasheet doesn't mention it, but still worth a try.

Tomorrow: Integrate accelerometer into control loop, test the ADC driver more extensively. Then remove unnecessary functions and write comments. Consider adding a string cmd to toggle relay, could be nice to be able to reset if the ADC triggers.

###260324
ADC integration complete, can now reliably store and read amps as a float. The shoulder motor seems to cut out at too high power settings, i.e. if the setpoint is too far away from current position. Need to figure that out, and should get to work on implementing a PID with proper timesteps over easter. Then ROS:)) Shoulder accelerometer feedback is implemented as part of joint update power. Hard coded for shoulder atm, but should be safe for other motors. Problem: The accelerometer reads 0 as soon as it passes 90 degrees, at least in the negative direction. This should be adjusted for somehow, e.g. by discarding/compensating for readings with a very high delta like in the motor driver.

Not finished with documentation, the joint controller is a brute. Made file headers with more extensive descriptions, looks neat in Doxygen.

###300324
Didn't bother commenting all the private functions of the joint controller. For PID control: simply set a timer interrupt for 10kHz and update control on a flag. Use error and previous error to do the D term. Tuning is pointless until the proper power supply is available. I term: avoid windup by zeroeing the term when error crosses 0, e.g. by XOR'ing error with previous error on poll.

Commenting is pretty much complete, shipping to Jo Arve for review.

Tomorrow:
1. Refactor motor driver to use a list of descriptors instead of the if 0/1 checks. Additionally, change the motor encoder define statements to 0 and 1 instead of 1 and 2.
2. Implement PID and very quickly test tuning.
3. Make a homing/startup/calibration algorithm. This will also introduce a global state variable, might justify another controller layer.

###310324
From yesterday: motor and encoder defines are based on hw silk designations, changed motor driver struct names to motor 1 and 2. Put them in a list, so correct indeces are still 0 and 1, respectively. This is still a bit unintuitive, and should probably be commented on.

PID implemented and tested for all joints. For I windup: only activate the I term when de/dt is less than 0.000017, corresponding to 10deg/sec or 0.17mm/sec. Strategy for tuning, which will probably still be relevant for the final voltage supply: Kp a bit higher than for the pure P controller. Kd 1/4 of Kp, and Ki 1/400 of Kp as initial values.

Rail homing OK, but needs 4V of force to even trigger the switch. Set up a state machine framework with error, idle, calibration and operating as global states, and one calibration state for each joint. Idea is to work through all individually, then stitch together in a sequence.

Briefly tried to set rise time and fall time for I2C to safe values for 400kHz and 100kHz (200, 1000 ns resp.) and tested on the hand onboard IMU on I2C3, but no luck.

###010424
Found a workable calibration scheme: Move until delta is 0, then move back a specified number of clicks, then stop and zero. It's becoming increasingly unintuitive that the joint position isn't actually used for anything.

Tried to use the scheme on elbow, effectively requiring power for both elbow and shoulder. There just isn't enought juice in the Mascot box for that, so will need to get the bigger power supply frist. If the box fries everything, at least I can start writing. Scratch that, the problem was that the torso mcu doesn't get updates from the shoulder mcu while its joints are calibrating. Solution: check for stale accelerometer data, and use the encoder.

While the method does seem to work, setting the total count to 0 only works from the set total count function. The zero function (formerly init) seems to set a random value. Calibration for all joints except shoulder tested.

Strategy for calibration procedure:
Make a new CAN filter with the upper bit active for global messages.
1. Torso starts by calibrating rail, setting global state to calib rail and emitting the appropriate CAN message.
2. Torso stablises shoulder in the vertical position, sets global state to twist clib when done.
3. Hand responds to global state by doing twist then pinch calib (setting states as it goes). Passes the buck to shoulder by setting global state wrist calib.
4. Shoulder requests 90 degrees on twist to ensure safe position (could also be set by hand immediately after calib), does wrist and elbow.

###030424
Something fundamentally wrong with how I manipulate endoder values. Zeroeing does not work as expected, but does something. Twist calib works if zero and set total is called at the beginning, but only set total at the end, and only if the joint has not moved away from its init position. I am updating the encodercount while in idle state, but that should have been zeroed by the zero function.

Calibration works. Rail calibration is not very robust, tends to go into a state of unsuccessfully sending CAN messages. Suspect the needle gets stuck, continuously triggering the interrupt and disturbing CAN trx. Safe-ish solution: place the rail almost at the end, just a few mm before the switch is triggered. Wrist also weakly coupled with the elbow, and for unknown reasons does not correct on its own. But it works! Should grease everything, then cover up. Possibly adjust rail to ramp up and down.

Set the power limit on shoulder and rail to 50 from 70, made it more stable. Really about time I integrated the real power supply.

###040424
Soldered the connector, seems to work. Deciding safe motor voltages: I have datasheets for all sizes of Pittman motors. Assuming "V1" is the voltage rating of the motor and trusting my work from the specialisation project:

Rail: 40mmx55mm 30.3V => Ipk=4.9A; KT=0.0472Nm/A
Shoulder: 54mmx113mm 30.V => Ipk=18A; KT=0.0972Nm/A
Elbow: 40mmx61mm 24V => Ipk=8.2A; KT=0.0365Nm/A
Wrist: 30mmx62mm 30V => Ipk=4.5A; KT=0.0272Nm/A
Twist/pinch (Escap): 23LT2R 12V => Imc=0.92A; KT=0.0124Nm/A

The 42V supply is not a viable option. For one, I broke the connector, and in any case it turns out even 30V is effectively too much. I got to use Finn's PeakTech 1535 laboratory switching mode power supply, which maxes out at 32V/20A. The regulators get very hot, so turned it down to 25 and re-tuned PID from there. Not fun, and got some strange instabilities because of it. The robot tried to beat itself to death several times.

1. The torso was effectively working at 50Hz because of my delay in main, probable cause for instability. It must have been just under a threshold previously, and at 30V it just crapped out.
2. Experimented with control schema. Rate limited PID, where udot is incorporated, could potentially work, but would need safeties to ensure that power could switch sign without penalty. Briefly considered changing to a pure velocity controller, but I don't know how I'd make it stop at the right position. And the current setup is not made for rate control, anyway.
3. Incorporated update_position into the loop. Error is now calculated from that, and previous position is also stored in case someone wants to use that later.Really need to make a "control loop" function/state, looks messy atm.
4. Need feedback on whether to focus on ROS or low level. If low level: incorporate torque calculations into ADC driver. Also divided the conversion constant by 10, ADC readouts look much more believable!

5. Need to prepare for integration with ROS. Go through every print statement and check that they are HMI only!

###050424
Implemented two CAN messages: JOINT_POS_REQ and JOINT_POS_TX as motor type messages. Syntax: data[0]=e/r, data[1..4]=clicks/rads. Motor number is masked out of ID in REQ and inserted back into TX. Torso should then be able to see all messages, but shoulder and hand only those relevant to their motors.

Removed a lot of dead code, but should still maybe remove functions that simply aren't in use. Tried compiling without string_cmd_parser, which didn't crash. Implies that uart messages are appropriately encapsulated in if-preprocs. Discovered that the accelerometer position must override the encoder position, because the encoder updates run so much faster than accelerometer updates.

I may just have fried the whole CAN circuit. In a completely unpredictable manner, the hand vbus caught while calibrating and were pulled out, and I'm not sure that power was decoupled in time before +25V hit CANL. Update: not fried

Need to disregard encoder data during calibration of shoulder joint. Tried overwriting encoder count in update_pos with accelerometer position and resolution, bu this introduces vibrations, likely due to interference between update_encoder_count in main and inaccuracy in the resolution estimation.

###090424
Wrote shoulder calibration procedure as effectively identical to update pos w/o the acc/enc check. It works, but is unstable if the elbow joint is extended at an acute angle. During operations, shoulder struggles with accuracy at high angles. Hypothesis: Too low voltage to effectively actuate the shoulder, and/or integral effect not strong enough. This is another reason for a velocity controller being preferable to a positional controller: the vc could have increased torque until the appropriate velocity was reached. Recommend keeping shoulder within +-1.2rad.

Also seeing that the calibration is not always successful, and that running it twice in a row does not necessarily work. This is probably due to the state machine having been tacked on top of an already complex system.

Stress test: Shoulder +-1.2rad when elbow at -1.5rad works well, maintaining good accuracy. Shoulder between 1.2rad and -0.5rad when elbow at 0 works well, but more noise audible around 1rad compared to elbow -1.5rad. Moving elbow from -1.5rad to 0 while shoulder at 1.2 rad makes shoulder droop temporarily. Hypothesis: low voltage makes the shoulder struggle to keep up during increased torque, and/or integral action too low.

For the thesis: Tune PID at voltage levels 20, 25, 30V using ZN, make qualitative assessment.

Downloaded ROS2 Humble Hawksbill, started following various tutorials. Got a bit ahead of myself, but rviz seems promising. Need to follow the tutorials to get a grip on TF, launcher scripts etc in the intermediate section after completing the beginner stuff.

###100424
Followed some of the intermediate lessons, but I think rviz and TF is a bit too heavy and can be automated by moveit. Moveit uses rviz, but has functionality to let me do motion planning etc.

###110424
Wrote URDF of the Orca, visualising using moveit and moveit setup assistant.
Problem:
1. 'Capabilities' error: launches.py line 203 changed with fix from [StackExchange](https://robotics.stackexchange.com/questions/110134/trouble-launching-moveit2-configurations)

2. 'Type double not string' error on rviz launch: [Locale problem](https://github.com/ros-planning/moveit2/issues/1049) , fix problem by starting command with LC_NUMERIC=en_US.UTF-8

3. Added acceleration and velocity limits for all joints, necessary for planning, in joint_limits.yaml, then rebuilt the project. Path planning works.

Phind suggests I use rviz/moveit to set up publishing of planned trajectories onto a topic, which a listening Serial node can then translate and send to UART. Need to find out if this is real-time or a "set" of commands.

###120424
Something broke towards the end yesterday after I started the tutorial for C++/MoveIt. One thing that almost certainly was wrong was that I installed the moveit package globally under Humble, as well as in the already existing build from source. Moveit complained about a double definition somewhere, anyway. Cleaned the slate and installed Iron instead. Building MoveIt on top of that resulted in fewer errors.

Created a package under code/ros called orca_moveit_config using setup assistant. Only changes made after setup was adding acceleration limits as floats (not ints!) to joint_limits.yaml. That means:
1. MoveIt is built from source under home/ws_moveit.

2. My orca package is built under ttk.../ros.

3. Useage requires sourcing ROS (automatically from bash), moveit (manually from ws_moveit) and orca_moveit (manually from ttk).

4. Launching the sim still requires LC_NUMERIC even though that was configured as part of the ROS install.

###130424
Everything exept reliable parsing of the input strings works. It seems completely random whether or not string comparison of the header makes it through.
Possible solutions: Everything happens in an interrupt handler, which is preempted by one of my many other timing interrupts etc. Will need to make a flag system or something. Alternatively, sophons are real. Frustrating as fuck.

Started writing a dedicated ROS message decoder, similar structure to CAN with flags etc. Problem: Only one joint pos setpoint mailbox, need to ensure that no positions are lost. Rewrite the CAN module to accommodate, or separate (FIFO) queueing structure in the ROS module?

Rewrite CAN module. Nbd. Added one message structure for dual positions, idea was to use that in conjunction with a queue system in the ROS module. However, KISS: add another message type s.t. one for shoulder and one for hand. Use filtering to ensure only one gets through at the relevant unit. queue_tx overwrites data in every instance, so setpoints will be lost if not transmitted. May result in more staccato movements, but that's OK.

Detailing the need for more messages: Joint setpoint only holds one position, and must be transmitted before the next setpoint is queued lest it be lost. ROS module receives (and sets) all setpoints at once -> would only send the last (i.e. wrist) for each ROS message received. Need to deal with that somehow. CAN messages can only be sent at 344Hz, so sending 4 positions consecutively at 100Hz is not possible (effectively 400Hz). If packing both setpoints in one msg, get 200Hz effectively, i.e. 2 msgs at 100Hz, which should be fine.

Rail and shoulder work smoothly with ROS integration! Tested with elbow only using the already existing joint setpoint message, works okay too but saw signs of bus contention: somewhat irregular shoulder movements (bad acc readings) and elbow was a bit jittery (slow/staccato movement). Granted, went straight to Operating state because I got tired of waiting for calibration.

###160424
All joints except pinch controllable from rviz. Run setup assistant again and reconfigure as there is something preventing the pincher from moving in rviz as it is. Set rail in its own planning group, noticed that the planner sometimes includes rail unnecessarily. Also increase maximum velocities and acceleration on everything except rail 2x, twist 5x.
----
Setup assistant couldn't find the urdf, and nobody else on the internet seems to get that particular error. Will need to find a workaround.
Options:
1. Set up ROS nodes to cooperate to send pinch data from terminal.
2. Modify string parsing to accommodate.
Went for 2., and set up a new function ros_interface_set_pinchPos accessed by string parser to set a static float in the ros module. Unfortunately, the compiler doesn't seem to recognize that one function. Could just need a reboot, could be because string parser and ros module are including one another. Cursed either way, should probably try 1. instead.

Set up another ros node Hmi to act as a substitute. Primarily to input the pinch command, but realised the STM ros module could just include the string parser to get full access to the string commands. Works, but currently does not solve the pincher problem. The issue is that I've set up the CAN cmds to update pincher implicitly, always setting it to 0. The manually typed pinch setpoint is overwritten every time the control_listener sends a set of setpoints.

###170424
The error went away after rebooting, now have full control. Observed that the shoulder does not always zero at vertical, unsure if that is due to poor PID tuning or inconsistent calibration.

Want to implement telemetry as a ROS node, as well as tuning PID parameters remotely.

Tried incorporating serial read as part of the serial_comms node using an infinite loop similar to the hmi node, but either that or the spin function will block the other. Will let that rest, and just keep using putty for reception for now.
Should probably still implement torque/current as telemetry!

Got a video and some screengrabs of Moveit, and hung a 500g weight on the gripper. The need for stronger PID tuning, probably even at a higher voltage, is clear: the arm struggles to find its setpoint, especially with higher weights. Really should try to up the voltage to 30V. Also attached some of the covers, which seems to have increased friction along with the application of sewing machine lube.

Tomorrow: PID tuning at various voltages, as well as performance evaluation. Should be way safer now that it follows positional setpoints with low deltas. Focus: increase I term. Also read the paper on tuning. Implement sending of telemetry such that current can be read from all joints. Will look good as a graph!

###180424
Skimmed the Skogestad paper on "The setpoint overshot method". Might try it, but it depends on the process overshooting its setpoint using a P controller. With the friction damping in this system, I don't think that's going to work.

Turned the voltage up to 30V with no other changes after homing. Noted a slight increase in ability to follow MoveIt references. In particular, elbow and wrist angles.

Testing tuning at 30V by disabling ROS and testing small deltas in positional setpoint in Putty.

SHOULDER/RAIL:
Changed volagepctcap from 70 to 100. No appreciable change in behavior: rail overshoots even at 10mm delta. 
Disabling maxmovementrate:

Shoulder oscillates for appr 25 seconds before settling after receiving delta of 0.3, 17 seconds at 0.1, and 7 seconds at 0.01. Note: incidentally lost CAN trx after the first try of 0.3, settled much faster then.

KpTi to 0.02 from 0.2: 15 seconds at 0.3, 10 seconds at 0.1, 2 seconds at 0.01.

Note: Aborting 30V, CAN bus keeps crapping out. Back to 25V

Kp to 40 from 30, 12 seconds at 0.3. Kp to 50, 10 seconds at 0.3. Kp to 60, 8 seconds at 0.3, 5s at 0.1, 1s at 0.01 no overshoot.

Note: went to state idle, shoulder started turning indiscriminately, moderately slow.

Rail oscillates, settles after 17s at delta of 300, 30s at 100, never really settles at 10. KpTi to 0.0002 from 0.0001: never settles at 10. Kp to 0.5 from 0.25: Overshoots once before settling at 10. The rail joint is characterised by highstatic friction, so almost any integral action will result in overshoot as the term winds up before the bogey moves at all -- then jerks. Doubling the Kp might have been risky, but should be fine for small deltas. Will find out when coupling rviz back on later.

ELBOW/WRIST:
Wrist is unstable after removing maxmovementrate check. Using the observation that KpTi for shoulder was approx 1/3000 of Kp, reducing wrist KpTi to 0.01 from 0.4: 7s at 0.3 due to slight overshoot. Increasing Kp to 50 from 40 due to high friction: Slight overshoot.

Increasing voltagepctcap to 100 and 95 from 70 and 57 for wrist and elbow, respectively: Wrist unchanged.
Increasing Kd to 25 from 20 in an attempt at lessening overshoot: No appreciable change in behavior.
Increasing KpTi to 0.02 from 0.01: 3s at 0.3, 1s at 0.1, 5s at 0.01.
Note: resists well to interference by me, although takes some time to kick in.
Increasing KpTi to 0.04 to improve resistance: 5s at 0.3, 3s at 0.1 (with some tail), no movement at 0.01. Resistance not notably improved, decreasing KpTi to 0.03.

Elbow oscillates w/o maxmovementrate. Zero is vertical.
Changing Kp 50 from 40, KpTi 0.01 from 0.15: 6s at 0.3, 3s at 0.1, no movement at 0.01. 
Kp to 60: 6s at 0.3, 5s at 0.1, no movement at 0.01.
Kp to 50, Kd to 20 from 12: 7s at 0.3.
Kd to 0: No change in behaviour, back to 12. Assuming this will be needed when gravity/load becomes a factor.

TWIST/PINCH:
Setting voltagepctap to 48 from 28 for twist and pinch.
Twist unstable, reducing KpTi to 0.01 from 0.8: 4s at 1.57, 1s at 0.1.
Main issue from previous RViz experiments was that twist would struggle to find its position, and maintain it under load. Increasing Kp to 40 from 30: 3s at 1.57, and noting that it resists sooner when I press at the end of the pincher.

Pinch: Don't know if integral action should be added. On the one hand, it should squeeze hard to lift whatever it is pinching, and adding I term will essentially ensure it is always at maximum when squeezing. On the other, it might take long to unwind when letting go.
Increasing KpTi to 0.01 from 0: Does squeeze, no apparent problem letting go.

All joints, with RViz: Finds positions more precisely than before, but overshoot some before finding the position. Problem: Tried moving rail while shoulder was at maximum, resulted in the arm slamming down. Hypothesis: accelerometer briefly crossed 90 deg, which is known to cause trouble. Path: reading is effectively lower than 90 deg, controller thinks it needs to increase paadrag to rectify, makes the problem worse. Solution: get an accelerometer which can read both y and z axes, do math on both axes to find actual angle

All joints, with RViz: Finds positions more precisely than before, but overshoot some before finding the position. Problem: Tried moving rail while shoulder was at maximum, resulted in the arm slamming down. Hypothesis: accelerometer briefly crossed 90 deg, which is known to cause trouble. Path: reading is effectively lower than 90 deg, controller thinks it needs to increase paadrag to rectify, makes the problem worse. Solution: get an accelerometer which can read both y and z axes, do math on both axes to find actual angle. This is FURTHER WORK for thesis. For now: restrict shoulder angle to 1.2, consider decreasing integral action. Elbow may also benefit from less integral action, as this joint also oscillates a bit. Alternatively, use both accelerometer and encoder data, which would require some serious improvements to movement handling. This is FURTHER WORK for thesis. For now: restrict shoulder angle to 1.2, consider decreasing integral action. Elbow may also benefit from less integral action, as this joint also oscillates a bit.

See images testpos_start and testpos_stop from rviz, compare with photos. Notably, the elbow is missing a few degrees. I suspect there is some degree of coupling between the shoulder and elbow, or more likely elbow and wrist, which becomes apparent at sharp angles. As the end position was found correctly, this somehow does not affect the encoder count (as opposed to the pinch/twist coupling)

Tried attaching the cover for the shoulder hardpoint. Discovered that the placement of the elbow encoder puts the wire in the way of the cover. Ditto motor wires. Not sure why, could be that the entire PCB was supposed to be 1 mm less wide on either side.

Attached a 750g bottle of water to the gripper. It lifts it approx 25cm with no issue, and carries it along the length of the rail. Twist counteracts swinging motion from the bottle as the rail starts moving. The arm finds its position cleanly and not much slower than with no load. Was able to put the bottle down once, gently. The second time the arm suddenly curled up as the bottle hit the table. Hypothesis: the sudden change in load scared it. Strange, as the controller running at 10kHz should be able to counteract this imo. 

Was not able to replicate the problem from before, but found a new one: CAN messages drop out from either moveit, control_listener or serial_comms intermittently. As the delta setpoint moves even while the messages are dropped, this causes a jolt in motion when the messages come back and the setpoint has suddenly moved far. Not sure what to do about it, but it may explain the previous crash.

###180424
Changing elbow KpTi to 0.005 from 0.01, Kd to 30 from 12.
The underlying issue is still windup. In an attempt at mitigating this, I'll implement a sigmoid function for KpTi:

g(x) = 1 - \frac{e^(75x-5)}{1 + e^(75x-5)},

which is 0.99 at 0 and 0.08 at 0.1 => The KpTi gain goes from 0 to 1 as the error becomes lower than 0.1 rads/mm. I suspect this might not be sharp enough, but I don't actually know how the error develops. If the error is never larger than 0.1 anyway, this is moot. It worked quite well, no visible overshoot in elbow.

Increasing wrist KpTi to 0.05 from 0.03. Finds calibration significantly better. IMPORTANT: Somehow, the wrist joint now stops at about -5 degrees, or 50 degrees "further" into the calibration movement than before. Wrist calibration has been increased accordingly, but this is seriously strange.

Flashing sigmoid remaining joints. Should see a less accurate, but more decisive rail joint as an error of 0.1mm is basically meaningless.

Turned the function off for wrist. Shoulder and elbow do become more stable, but at the loss of accuracy. Likely the integral error never kicks in.
Reducing width argument to 40 from 75. The gain is then 0.02 at 0.2rad/11deg, and 0.55 at 0.1rad/6deg. No discernible change in behavior.

Reducing argument to 30, gain 0.16 at 0.2, 0.8 at 0.1. This seems to be a marginal improvement, and gives me something to write about. Should consider trying to get joint data out via the joint request message. Could for instance write positional data from one joint at a time to two different files, then concat in excel.

The 750g bottle test failed pretty hard, elbow and wrist were clearly drooping. Set the argument to 20, which gives 0.05 at 0.4, 0.73 at 0.2 and 0.95 at 0.1. This majorly improved performance, almost no droop in elbow. Turning it on again for wrist, and increasing KpTi to 0.07 from 0.05. Performance seems to improve for wrist.

The bottle test is OK. Lift it up, carry it across the desk, put it down. Then I poke the hand to ground myself, and the arm instantly curls up: elbow and shoulder go to maximum extension. I saw this yesterday too, so I don't think it's related to the sigmoid. Maybe check the function's output for ![-1,1]? The CAN bus has been reliable since I turned the voltage down, so shouldn't be that. In any case, at least for the shoulder joint, LOS with the accelerometer shouldn't be lethal. Wish I had telemetry!

Tomorrow: Make a gripper.
Next week: Comment ROS code, do a cleanup s.t. there are no (or very few) problems with the code during build. Then start writing the thesis. Consider implementing telemetry for data capture if it seems like a good idea by the end of the week.

###250424
Spent the last few days ill with something.
Discovered that the shoulder never broadcast global state operating after elbow calib, so both hand and torso were in their calibration states. This is another proof that the state machine is whack.

The shoulder joint keeps acting up. I suspect it's much because the acc input isn't filtered, which could explain why it has such a poor perturbation step response (aka spazzes out as soon as something touches it or leaves the gripper). The calibration also doesn't work, measured correct offset at the start of calibration before suddenly very low offset. These are probably related.

Hypothesis: the accelerometer measures a jolt when the shoulder either starts moving on its own or is perturbed by the gripper dropping whatever it's holding. For the calibration phase, this means it exits prematurely as the measured error suddenly becomes low. For when the gripper drops something or I knock on it, the same happens and the error momentarily increases. This makes the controller freak out.

It doesn't really make sense. Direction of forces means the acc should measure increased acceleration (equating to greater error) when the arm starts moving. Additionally, large changes in error is unproblematic when coming from MoveIt, as I discovered when I accidentally left it in a crouched position right after calibrating the physical arm.

Also added a timer interrupt on timer7 for telemetry, 50Hz. Currently sends shoulder pos, sp and current. Got fairly good data for grabbing and dropping bottle, and susequent spazzing.

Set hasAccelerometer to 0 for shoulder. The arm is now quite stable, strengthening the hypothesis.

###240524
Added test logs for main loop time and shoulder movement.
Used timer6 with a prescaler of 0, probably about 180us per main loop.
main loop.log: disregard, prescaler of 18.
main loop 0psctim.log: initial test with prescaler of 0 in idle state and no input.
main loop idle receiving moveit: idle state, receiving state updates from moveit.
main loop oper receiving moveit: operational state, receiving orders from moveit.
shoulder 0.7 elbow 1.5: moving shoulder to 0.7 rads and elbow to 1.5 rads. Telemetry from shoulder only.
shoulder 0.7 elbow 1.5: shoulder to 0.7 rads while elbow is const 1.5 rads.
shoulder 0.7 elbow ext: shoulder to 0.7 while elbow is fully extended.

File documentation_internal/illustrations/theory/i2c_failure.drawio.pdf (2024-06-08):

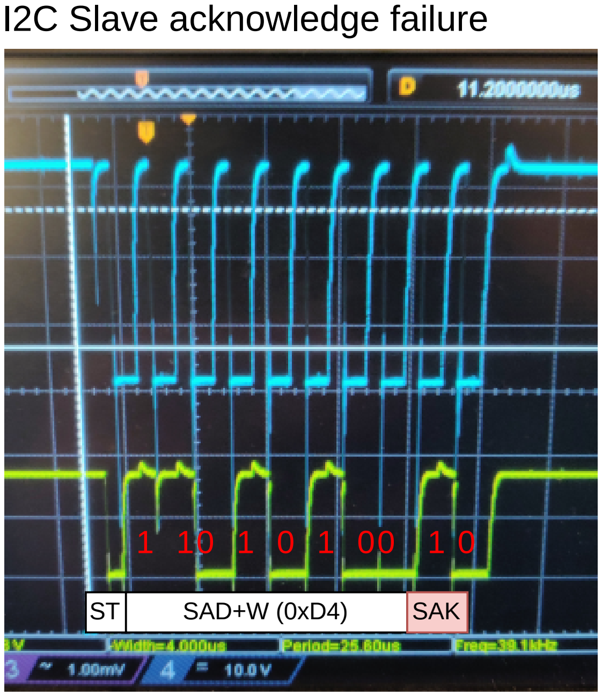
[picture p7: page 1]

I2C Slave acknowledge failure

ST | SAD+W (0xD4) | SAK

1 10 1 0 1 00 1 0

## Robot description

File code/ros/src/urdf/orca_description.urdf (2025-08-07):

<?xml version="1.0"?>
<robot name="ttk4900_orca">
  
  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
  
  <link name="base_link">
    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
  </link>

  <link name="torso_link0">
    <inertial>
      <origin xyz="0.0 0.0 0.0" rpy="0.0 0.0 0.0"/>
      <mass value="8.0"/>
      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
    </inertial>
    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
  </link>

  <link name="torso_link1">
    <inertial>
      <origin xyz="0.0 0.0 0.0" rpy="0.0 0.0 0.0"/>
      <mass value="0.2"/>
      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
    </inertial>
    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
  </link>

  <joint name="joint_base_torso" type="prismatic">
    <origin xyz="-0.9 0.0 0.045" rpy="0.0 0.0 0.0"/>
    <parent link="base_link"/>
    <child link="torso_link0"/>
    <axis xyz="-1 0.0 0.0"/>
    <limit lower="-1.40" upper="0" effort="100" velocity="0.1"/>
  </joint>

  <joint name="joint_t0t1" type="fixed">
    <origin xyz="0.11 0.0 0.12" rpy="0.0 0.0 0.0"/>
    <parent link="torso_link0"/>
    <child link="torso_link1"/>
    <axis xyz="0.0 0.0 0.0"/>
    <limit lower="0.0" upper="0.0" effort="0.0" velocity="0.0"/>
  </joint>

  <link name="link_upper_arm">
    <inertial>
      <origin xyz="0.0 0.0 0.0" rpy="0.0 0.0 0.0"/>
      <mass value="2.5"/>
      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
    </inertial>
    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
  </link>

  <joint name="joint_torso_upper_arm" type="revolute">
    <origin xyz="0.0 0.0 0.09" rpy="0.0 0.0 0.0"/>
    <parent link="torso_link1"/>
    <child link="link_upper_arm"/>
    <axis xyz="-1 0.0 0.0"/>
    <limit lower="-1.5" upper="1.5" effort="100" velocity="0.17"/>
  </joint>

  <link name="link_lower_arm">
    <inertial>
      <origin xyz="0.0 0.0 0.0" rpy="0.0 0.0 0.0"/>
      <mass value="1.5"/>
      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
    </inertial>
    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
  </link>

  <joint name="joint_upper_lower_arm" type="revolute">
    <origin xyz="0.035 0.0 0.24" rpy="0.0 0.0 0.0"/>
    <parent link="link_upper_arm"/>
    <child link="link_lower_arm"/>
    <axis xyz="1 0.0 0.0"/>
    <limit lower="-2.5" upper="2.5" effort="100" velocity="0.17"/>
  </joint>

  <link name="link_hand">
    <inertial>
      <origin xyz="0.0 0.0 0.0" rpy="0.0 0.0 0.0"/>
      <mass value="0.5"/>
      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
    </inertial>
    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
  </link>

  <joint name="joint_lower_arm_hand" type="revolute">
    <origin xyz="-0.015 0.0 0.245" rpy="0.0 0.0 0.0"/>
    <parent link="link_lower_arm"/>
    <child link="link_hand"/>
    <axis xyz="-1 0.0 0.0"/>
    <limit lower="-8" upper="2.5" effort="100" velocity="0.17"/>
  </joint>

  <link name="link_twist">
    <inertial>
      <origin xyz="0.0 0.0 0.0" rpy="0.0 0.0 0.0"/>
      <mass value="0.2"/>
      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
    </inertial>
    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
  </link>

  <joint name="joint_hand_twist" type="continuous">
    <origin xyz="-0.0325 0.0 0.042" rpy="0.0 0.0 0.0"/>
    <parent link="link_hand"/>
    <child link="link_twist"/>
    <axis xyz="0.0 0.0 1"/>
    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
    <limit effort="100" velocity="3"/>
  </joint>

  <link name="link_gripper0">
    <inertial>
      <origin xyz="0.0 0.0 0.0" rpy="0.0 0.0 0.0"/>
      <mass value="0.03"/>
      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
    </inertial>
    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
  </link>

  <joint name="joint_twist_gripper0" type="prismatic">
    <origin xyz="0.0 0.0 0.023" rpy="0.0 0.0 0.0"/>
    <parent link="link_twist"/>
    <child link="link_gripper0"/>
    <axis xyz="-1 0.0 0.0"/>
    <limit lower="0.0" upper="0.04" effort="100" velocity="0.01"/>
  </joint>

  <link name="link_gripper1">
    <inertial>
      <origin xyz="0.0 0.0 0.0" rpy="0.0 0.0 0.0"/>
      <mass value="0.03"/>
      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
    </inertial>
    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
  </link>

  <joint name="joint_twist_gripper1" type="prismatic">
    <origin xyz="0.0 0.0 0.023" rpy="0.0 0.0 0.0"/>
    <parent link="link_twist"/>
    <child link="link_gripper1"/>
    <axis xyz="1 0.0 0.0"/>
    <limit lower="0.0" upper="0.04" effort="100" velocity="0.01"/>
  </joint>


</robot>

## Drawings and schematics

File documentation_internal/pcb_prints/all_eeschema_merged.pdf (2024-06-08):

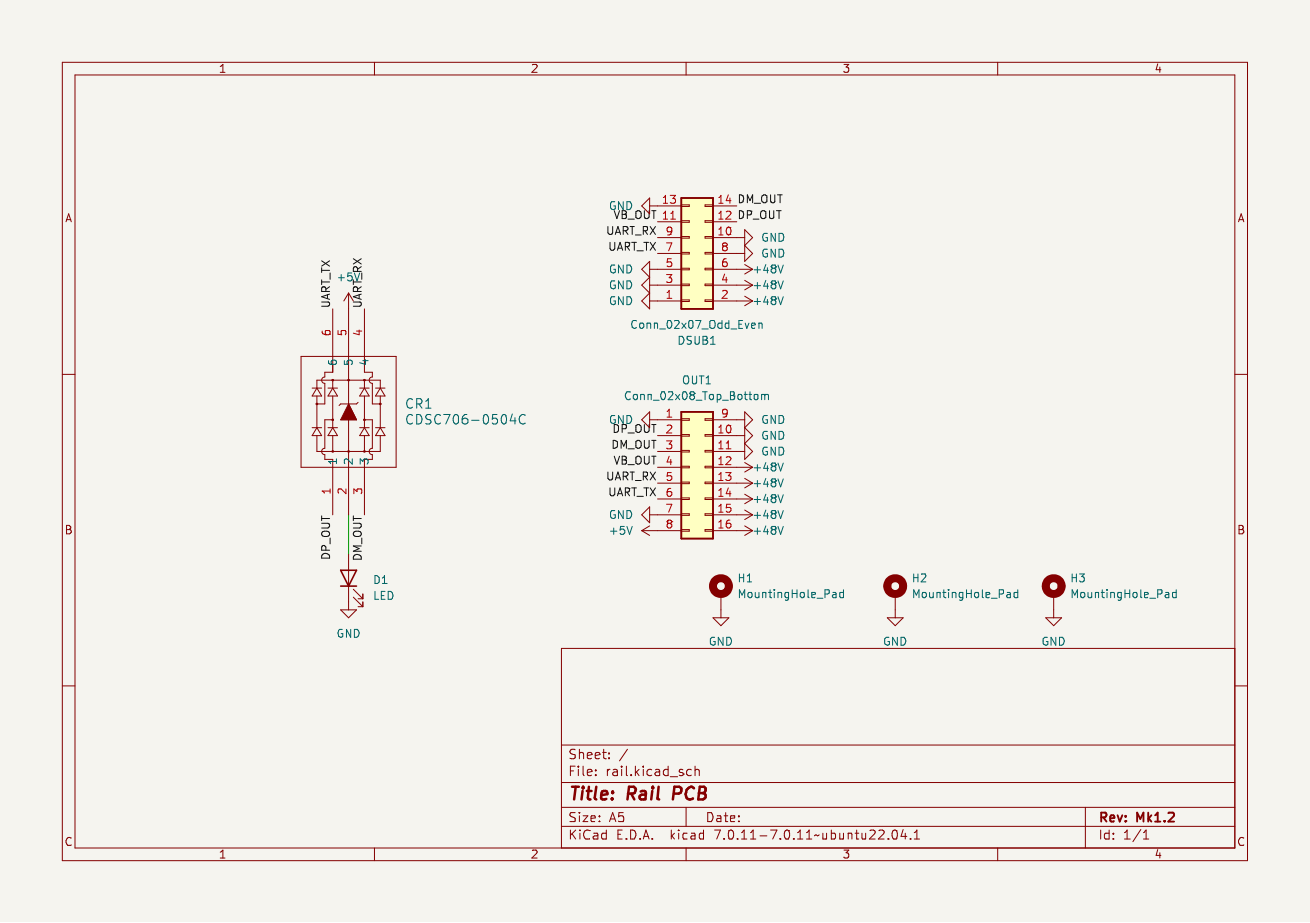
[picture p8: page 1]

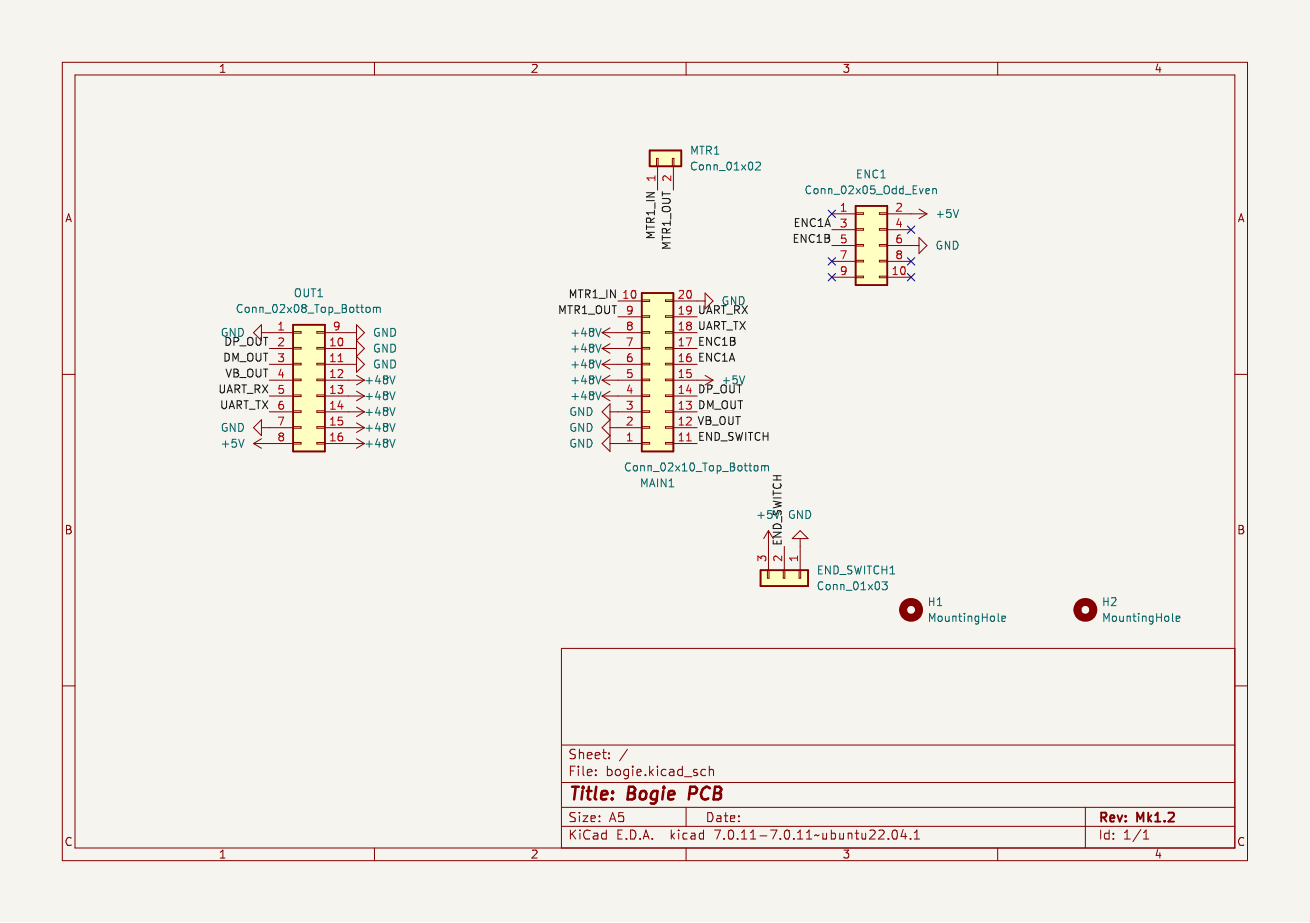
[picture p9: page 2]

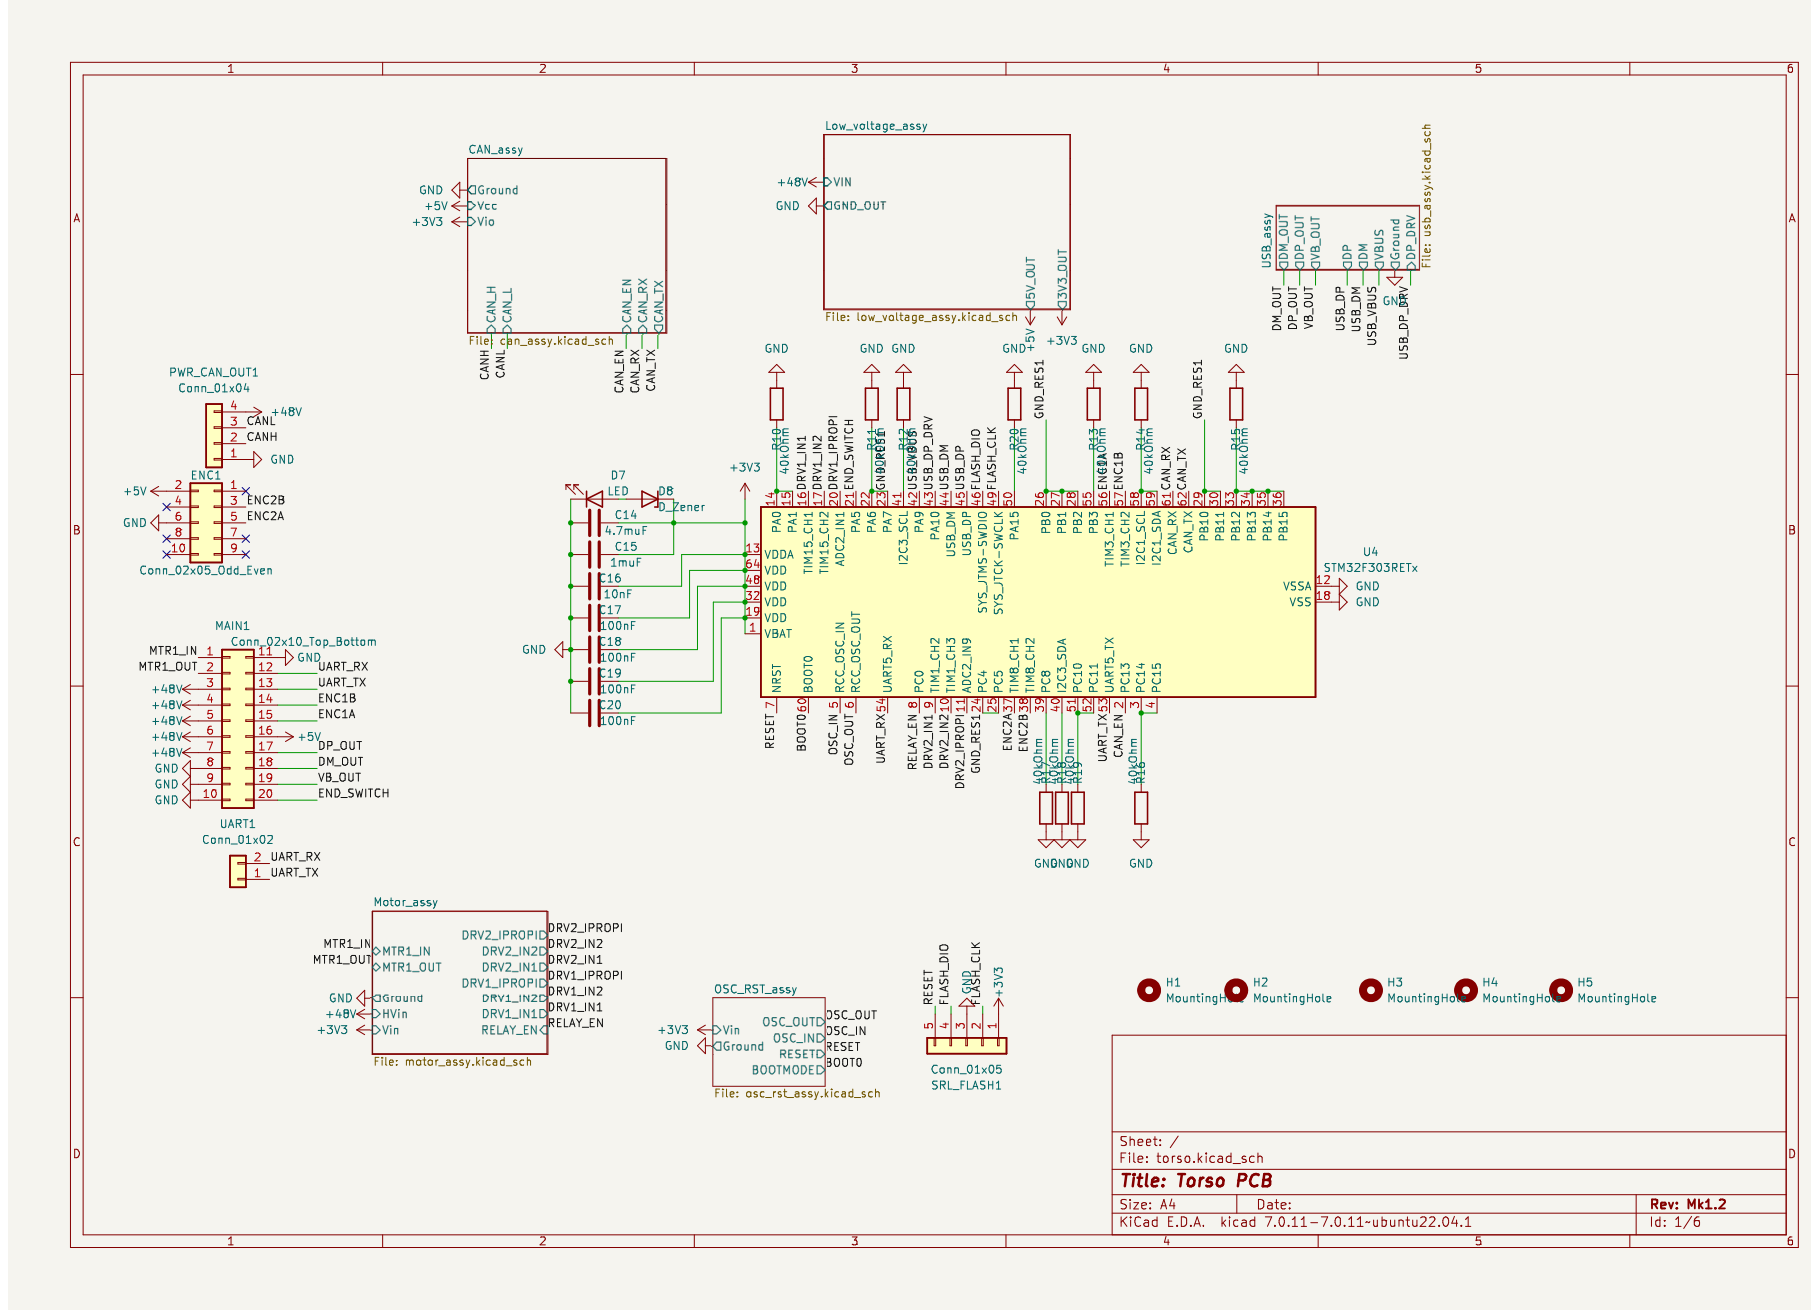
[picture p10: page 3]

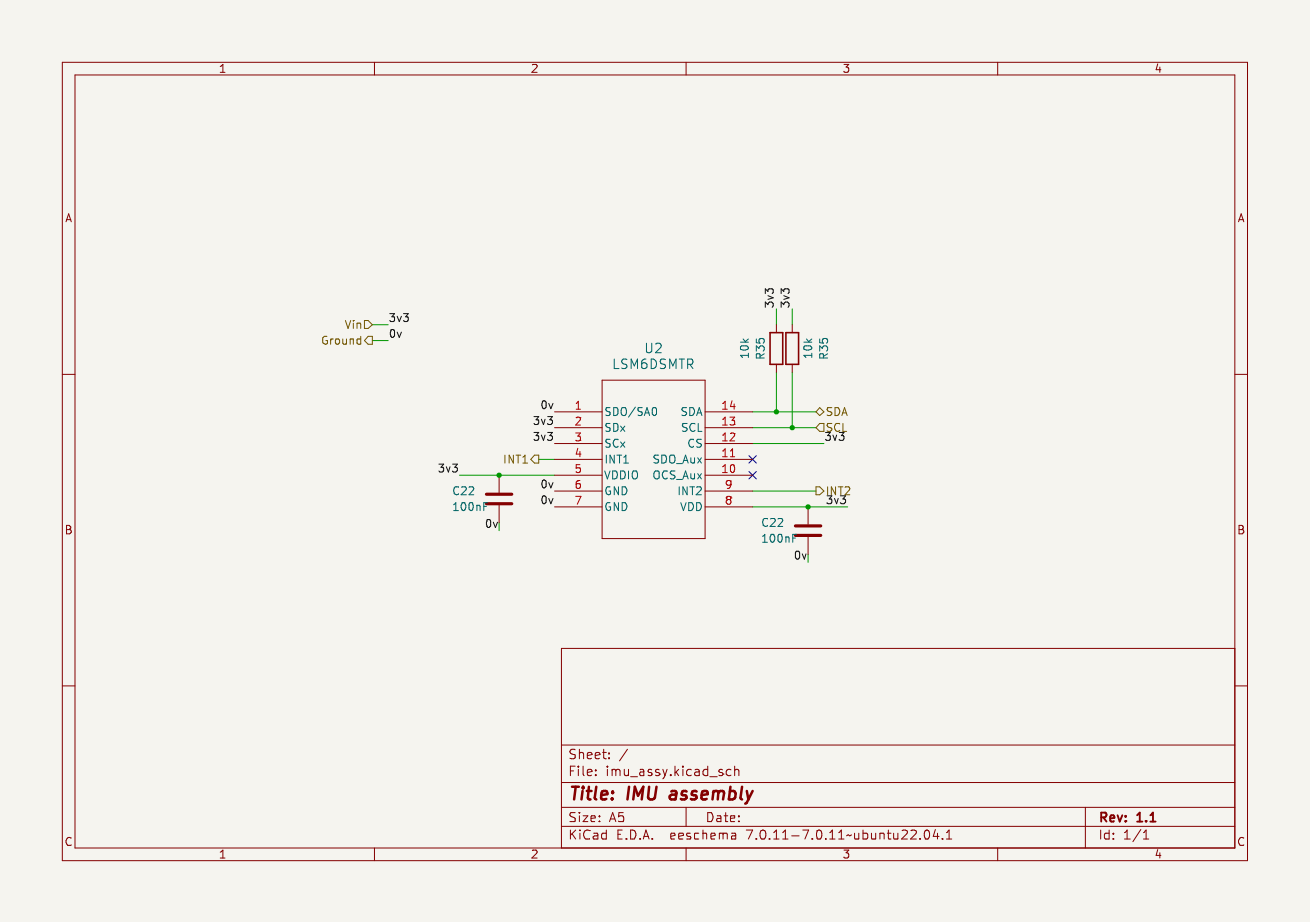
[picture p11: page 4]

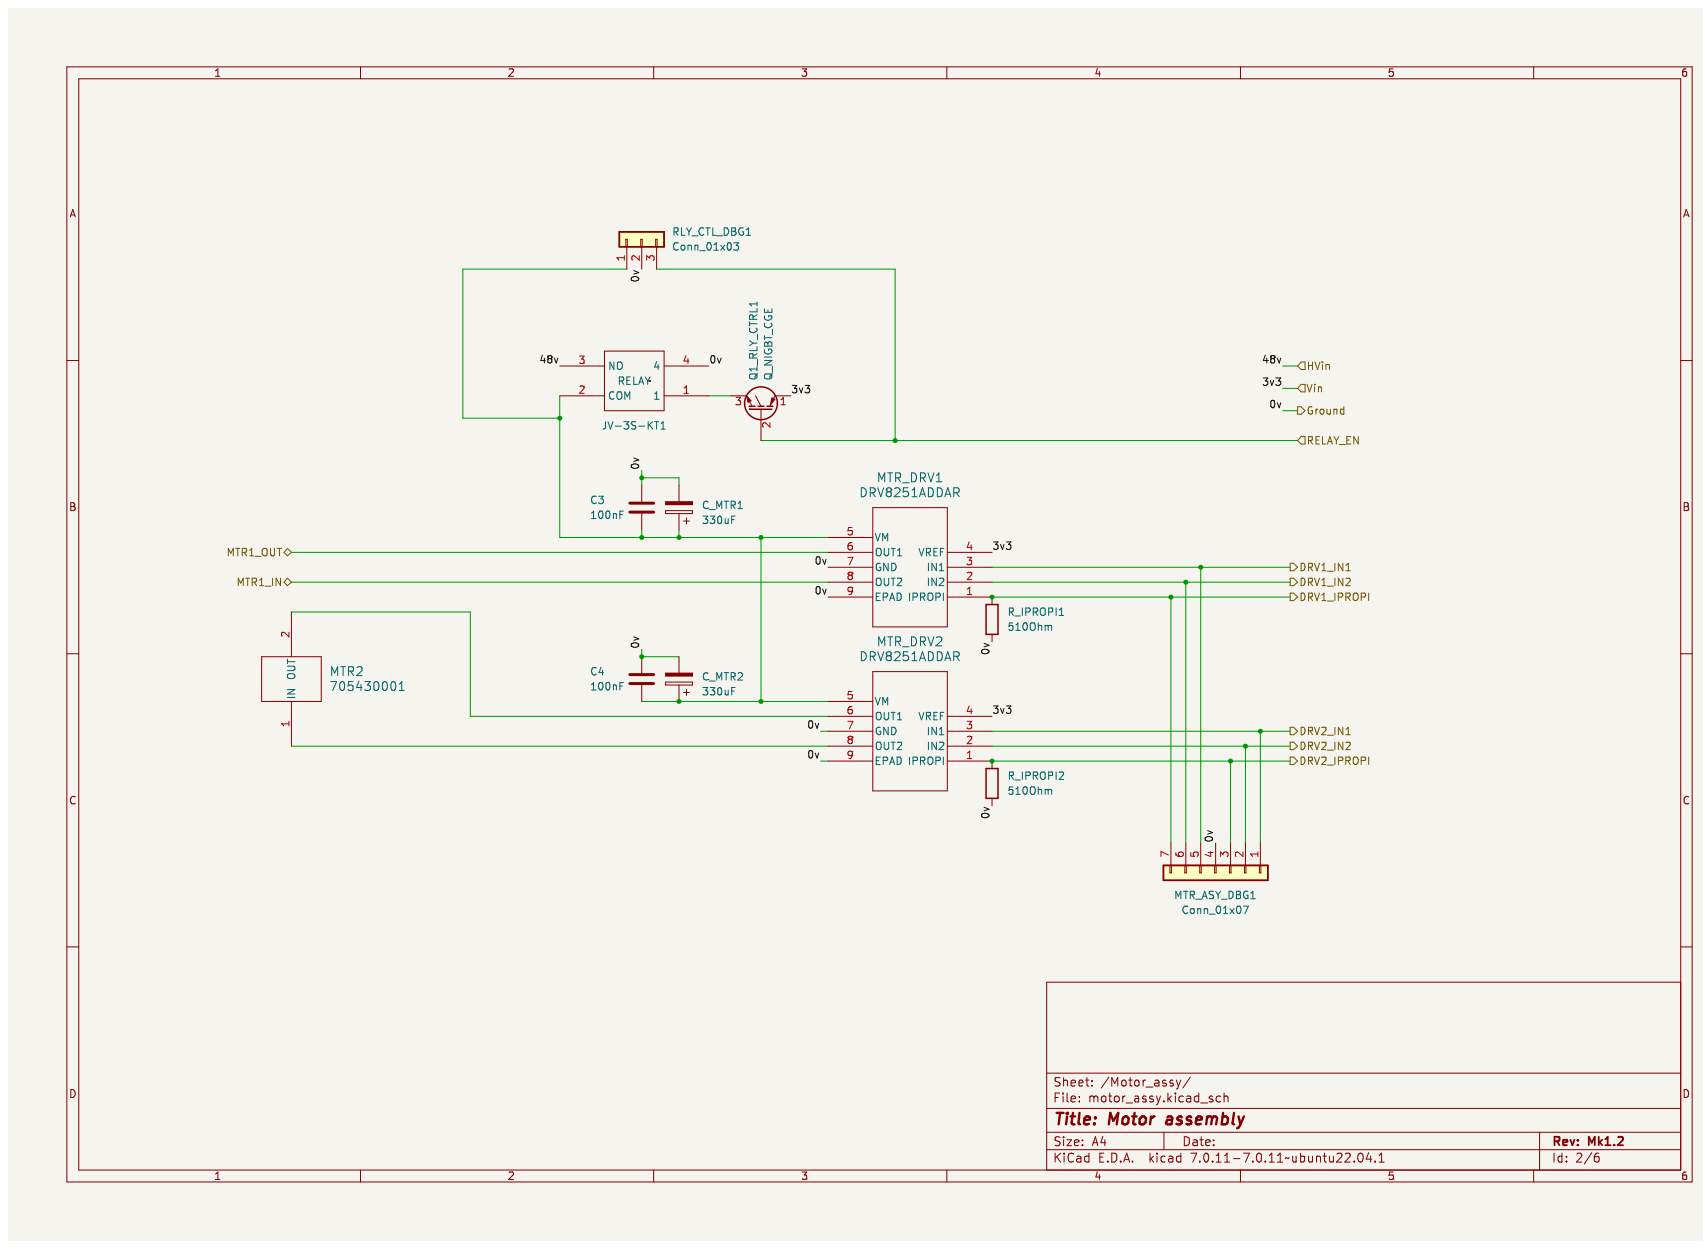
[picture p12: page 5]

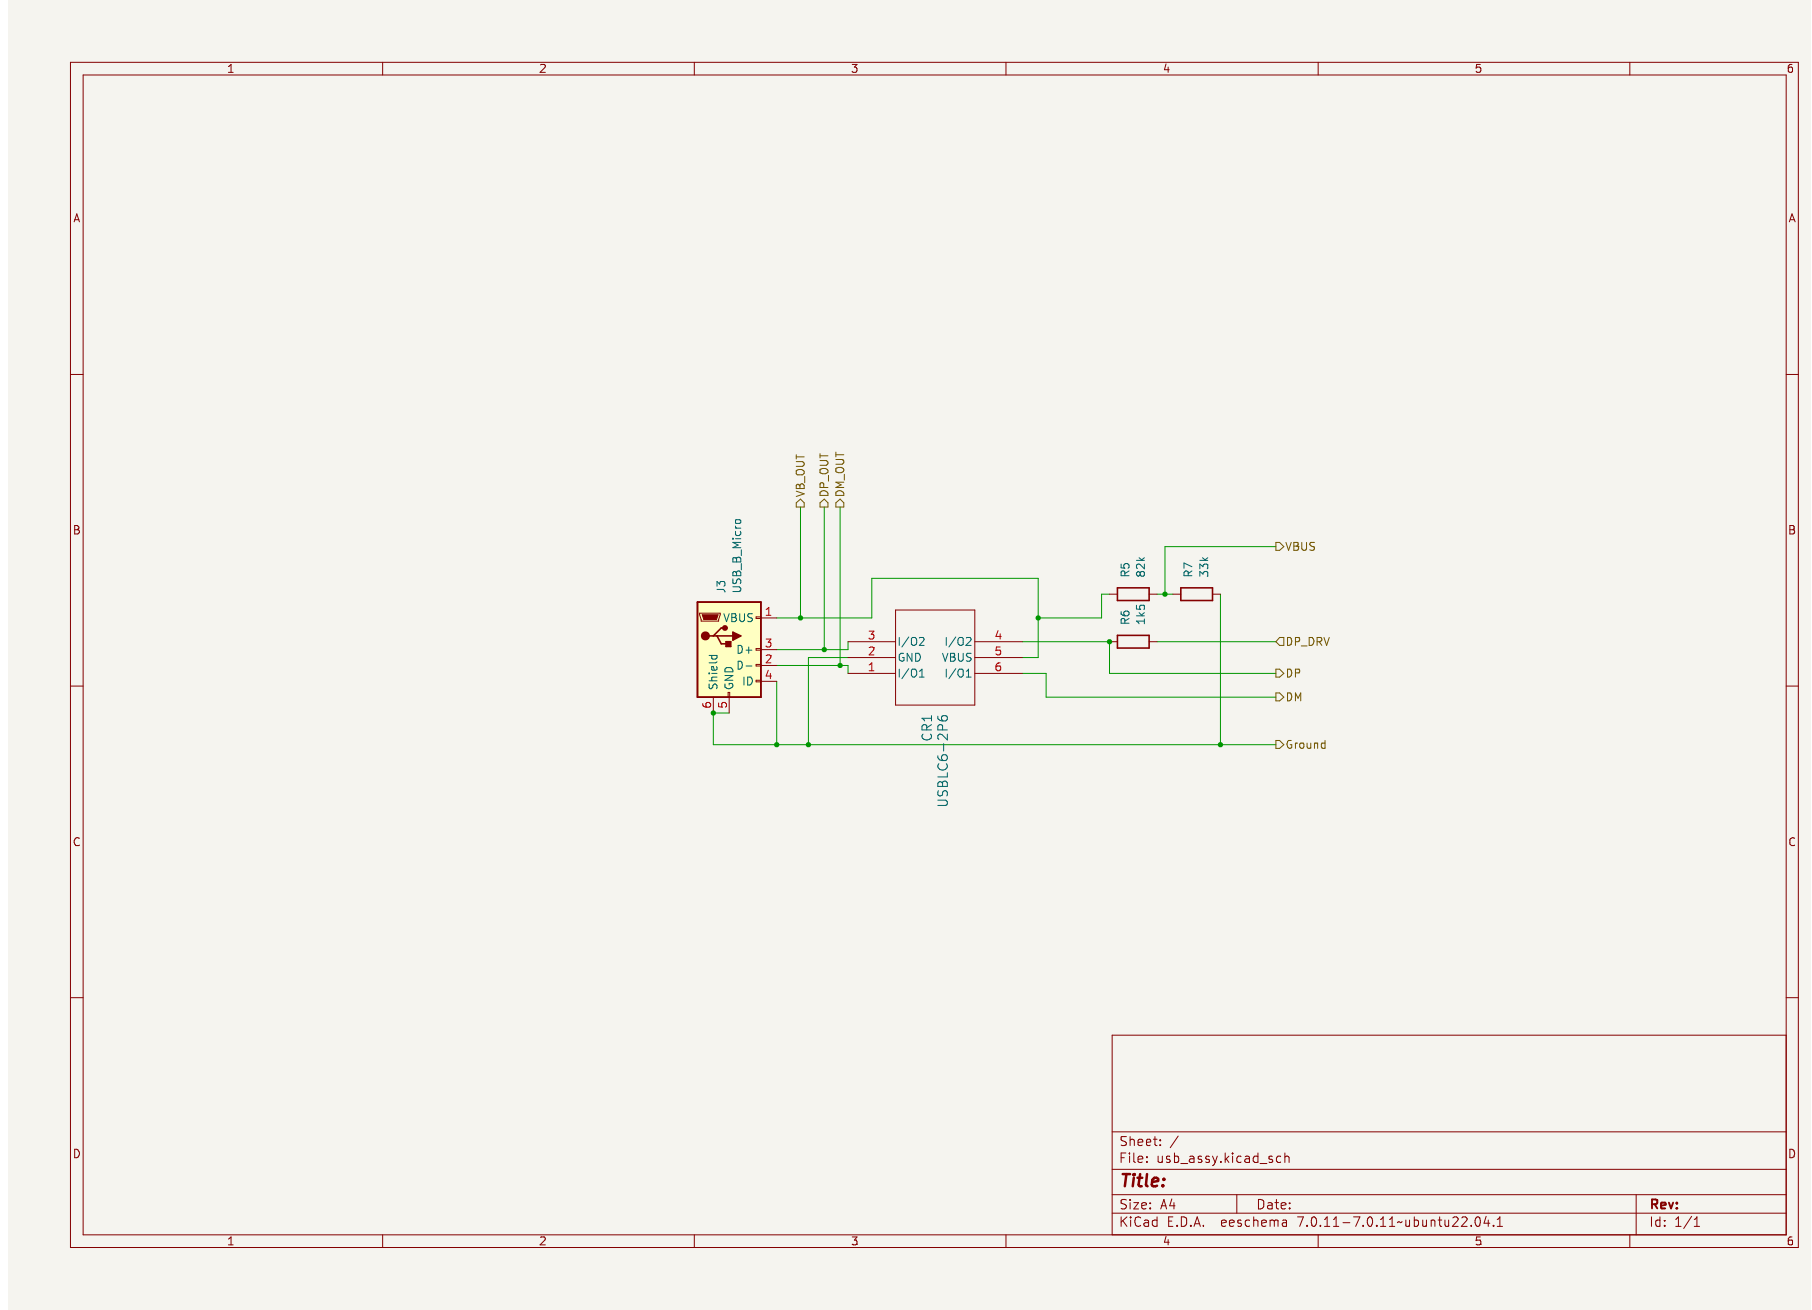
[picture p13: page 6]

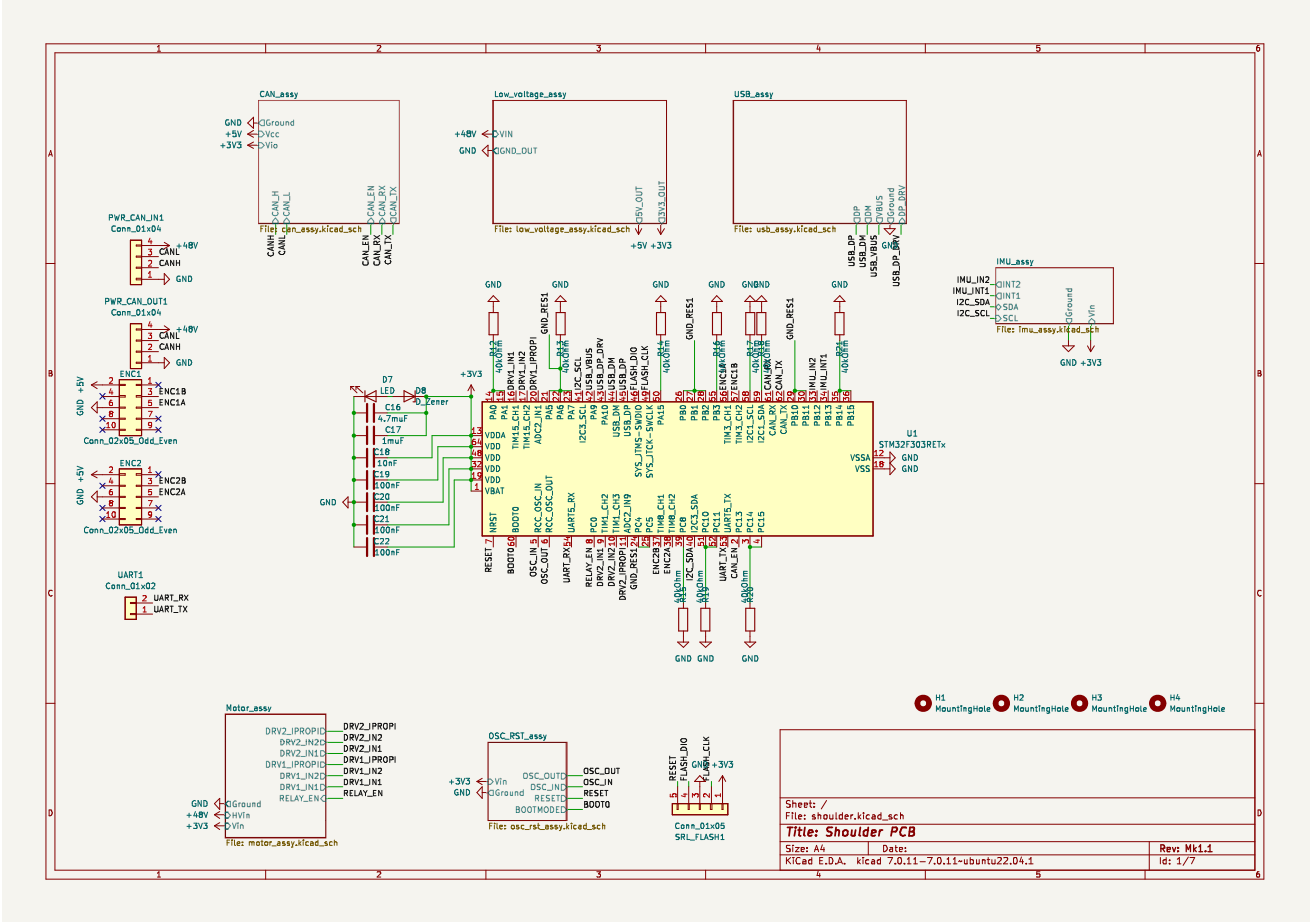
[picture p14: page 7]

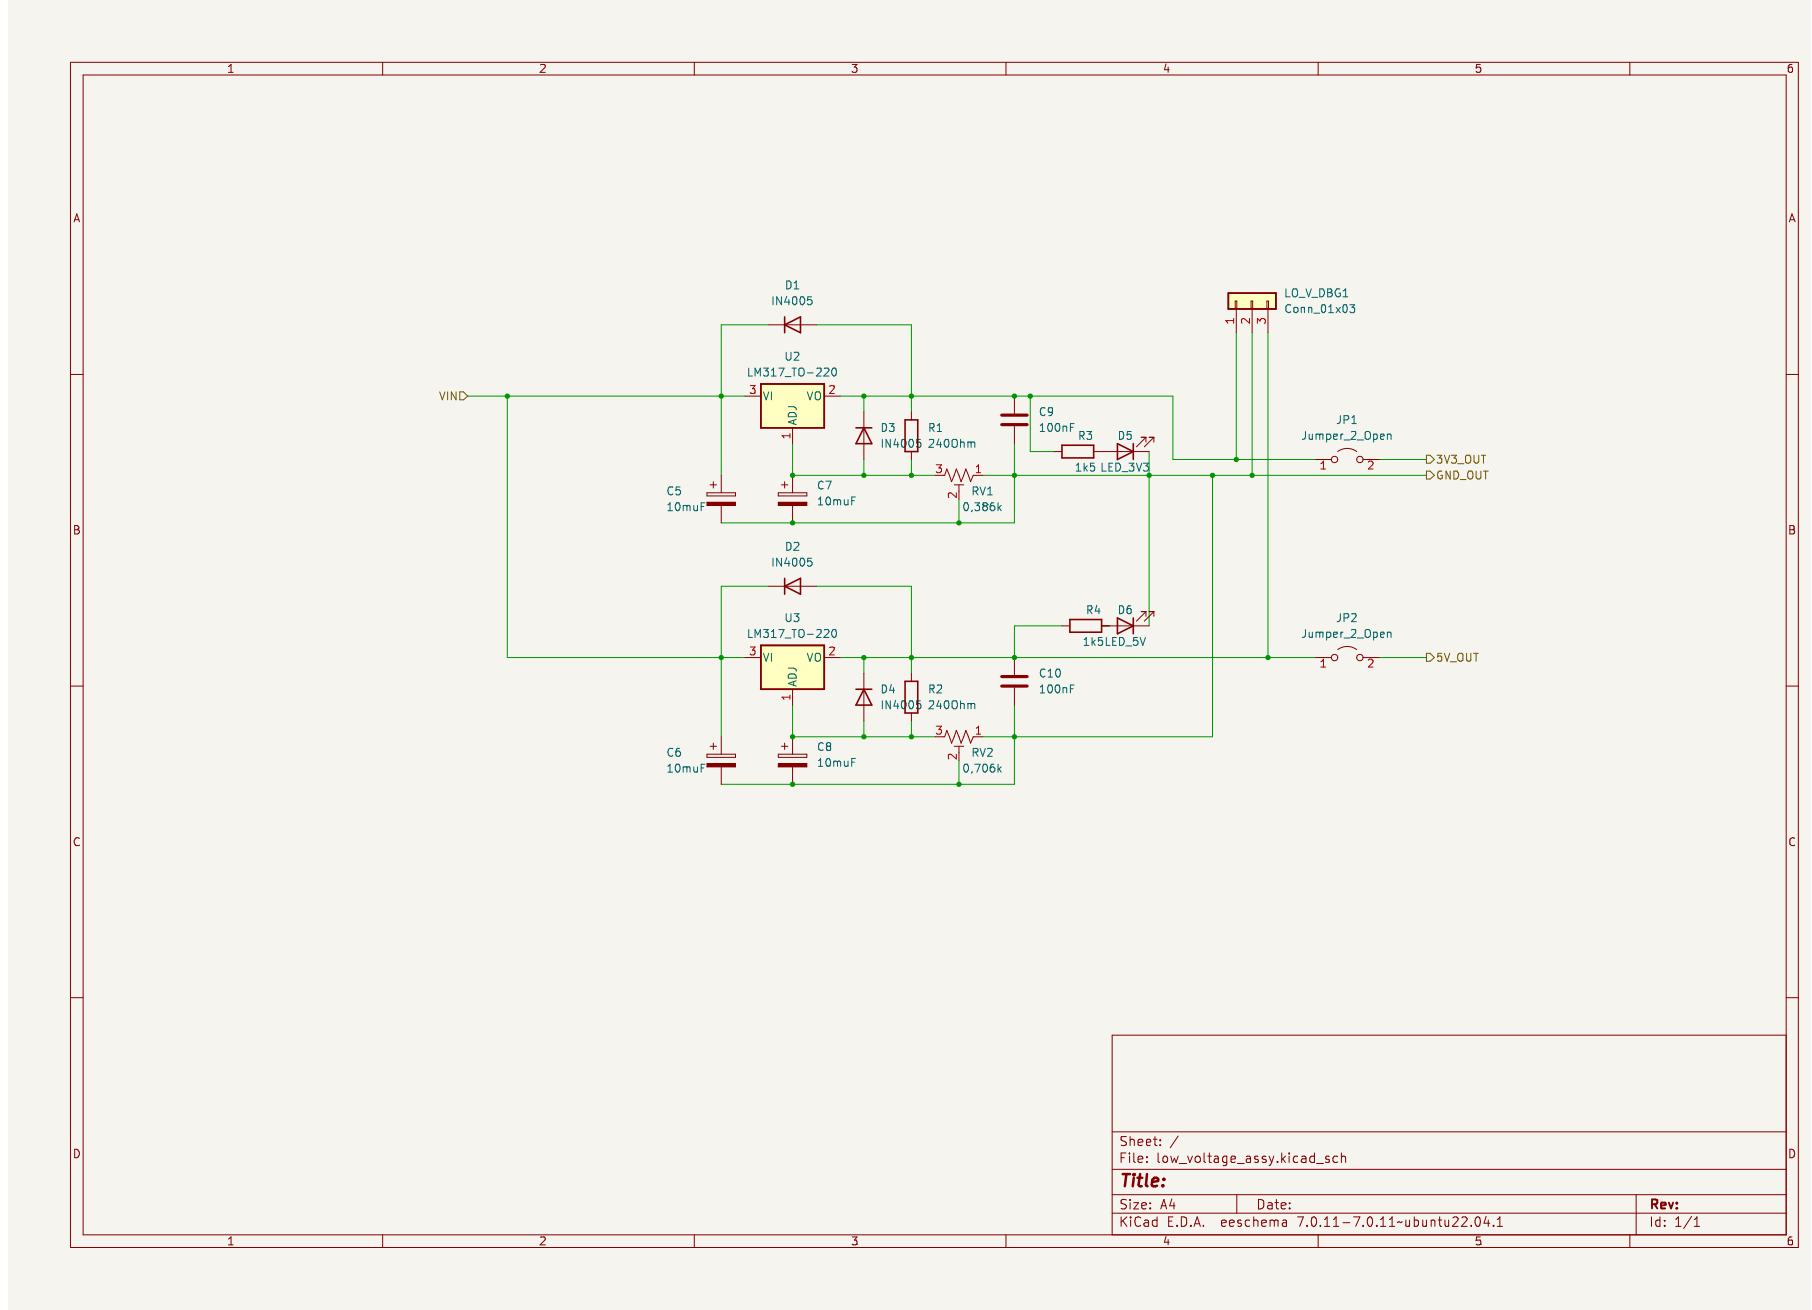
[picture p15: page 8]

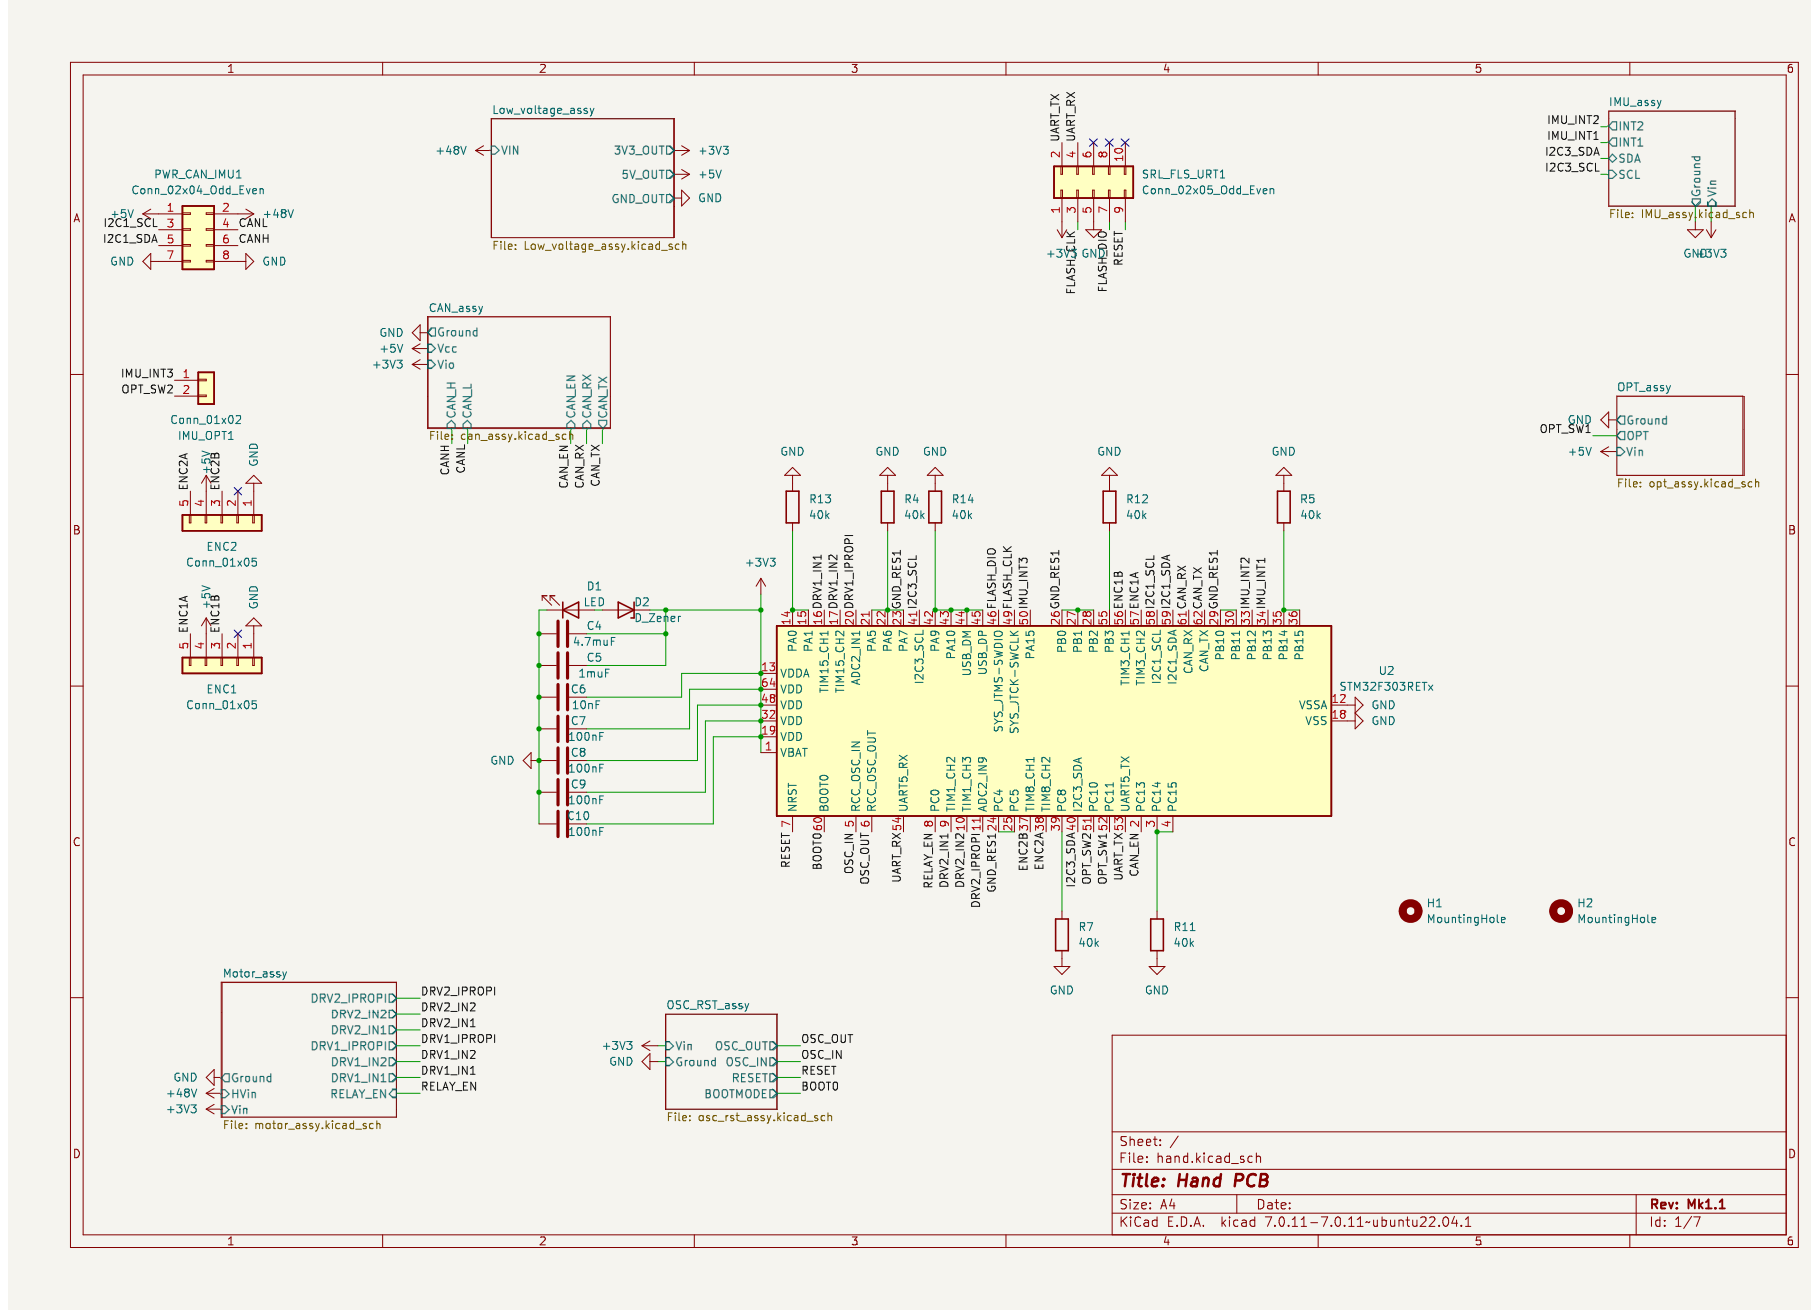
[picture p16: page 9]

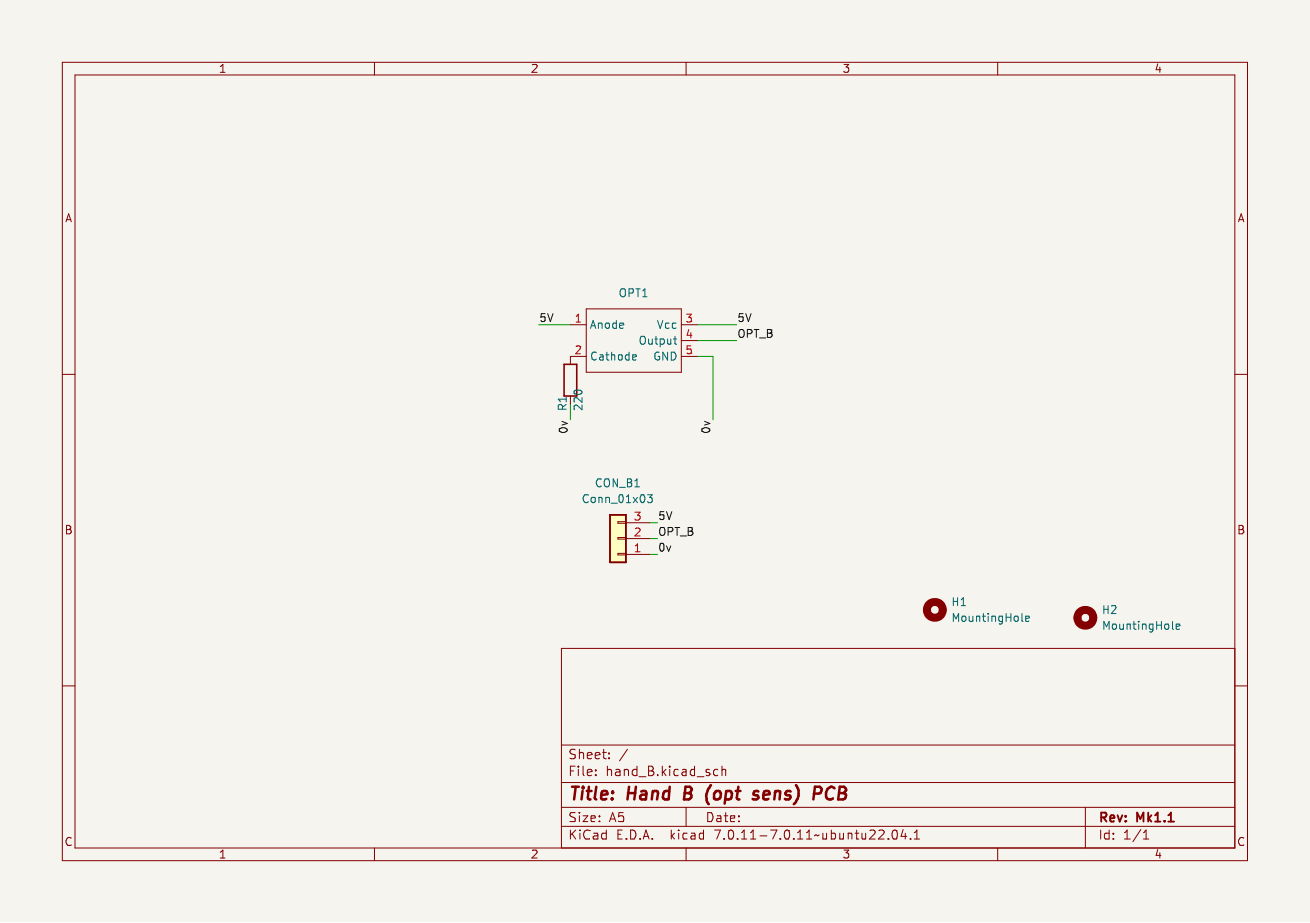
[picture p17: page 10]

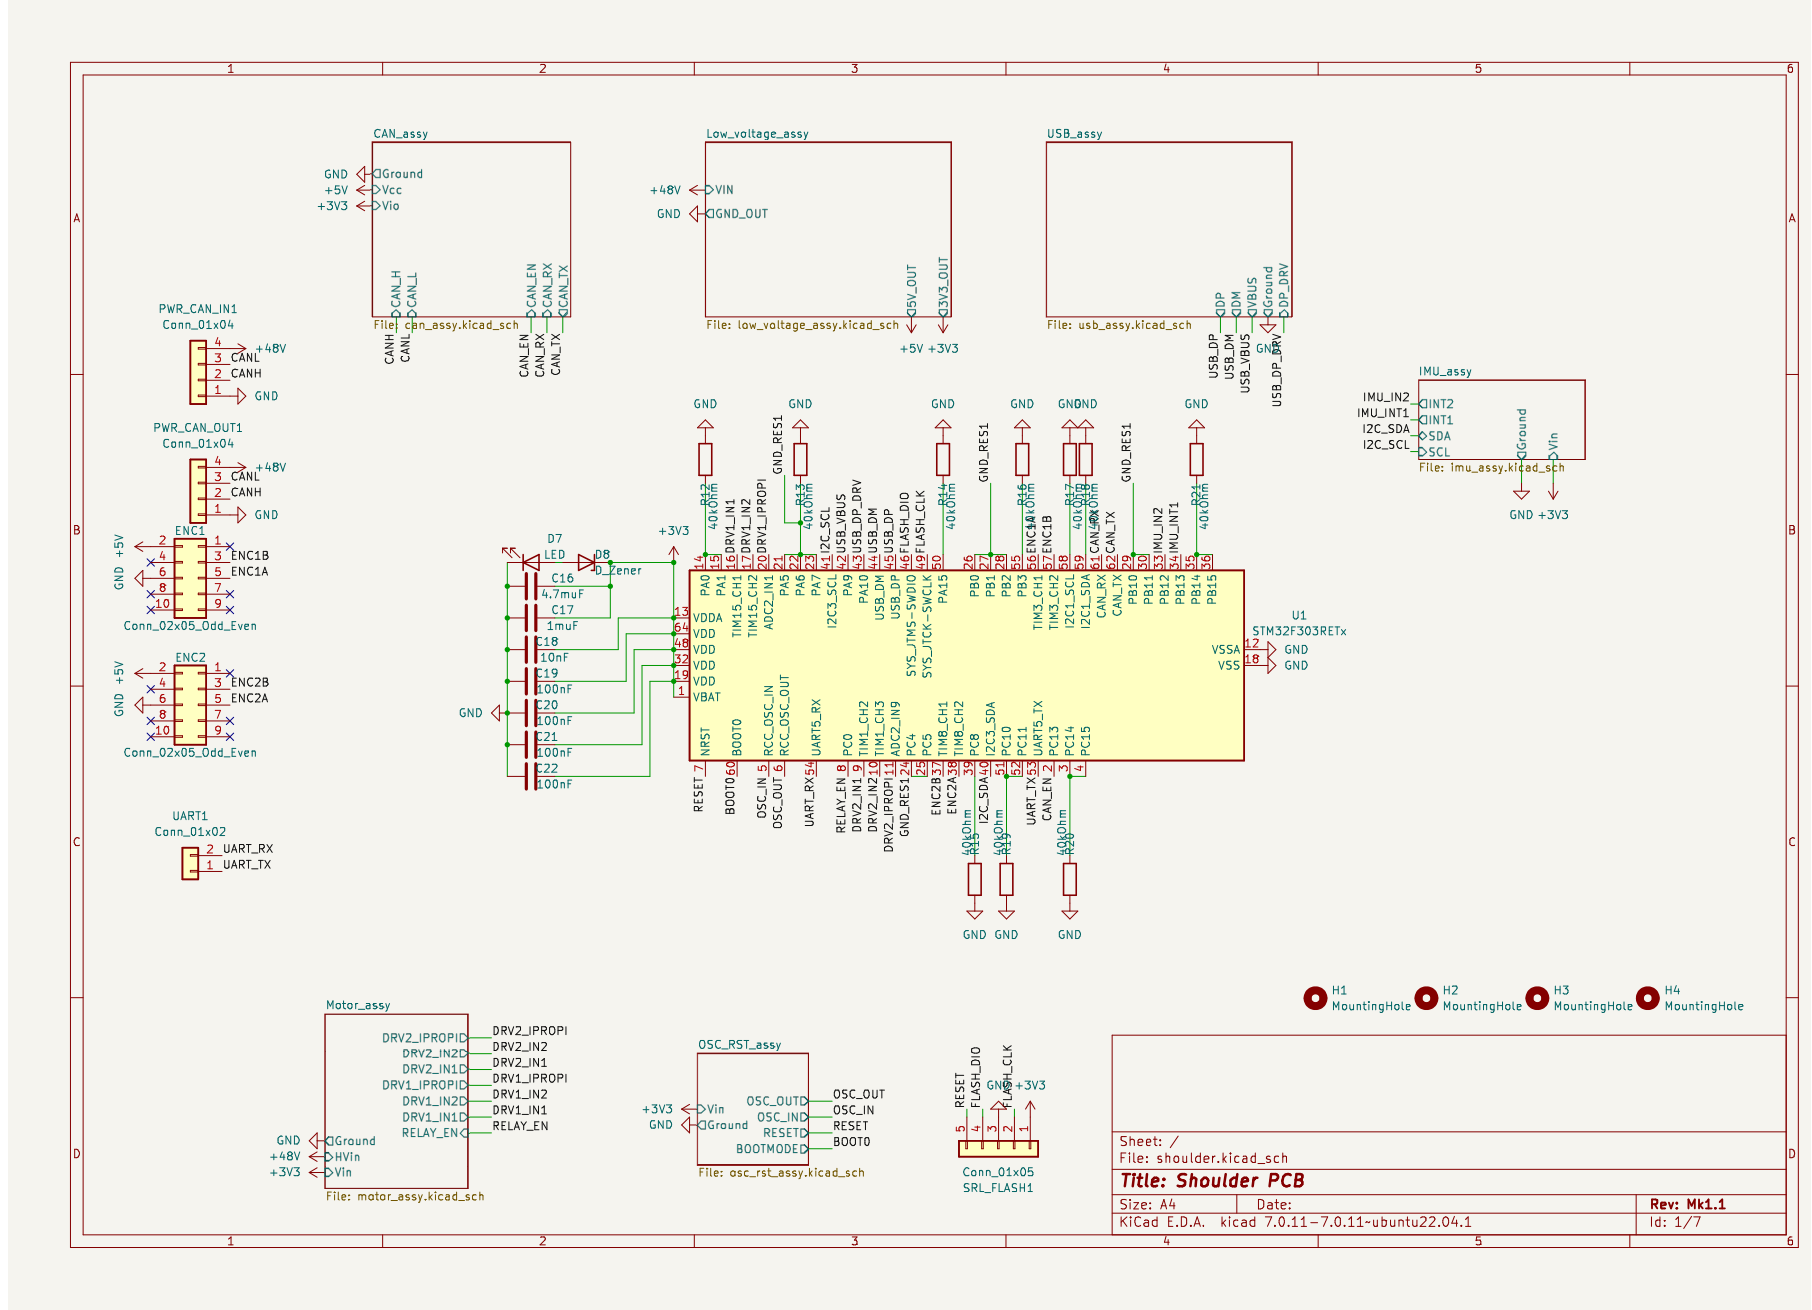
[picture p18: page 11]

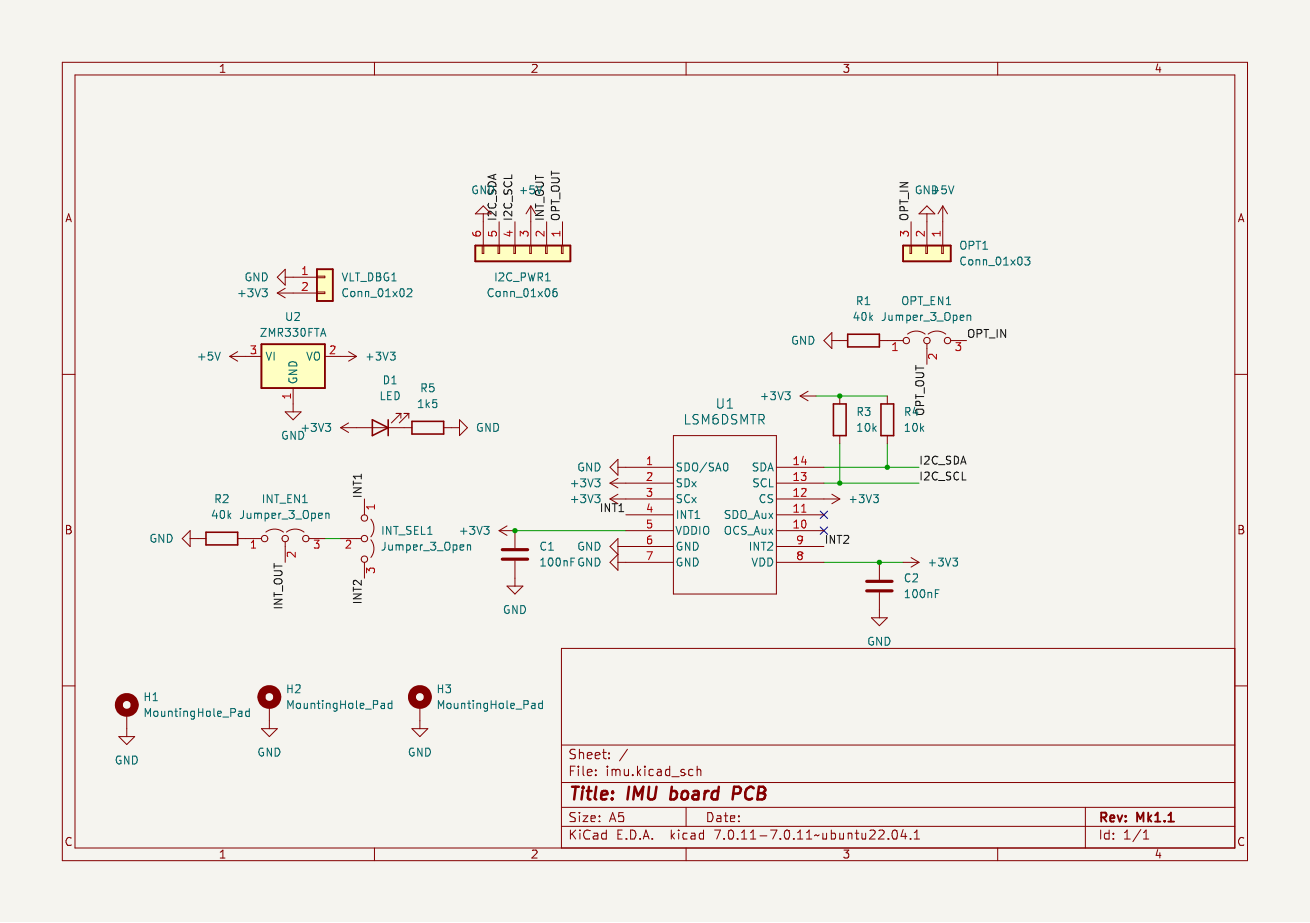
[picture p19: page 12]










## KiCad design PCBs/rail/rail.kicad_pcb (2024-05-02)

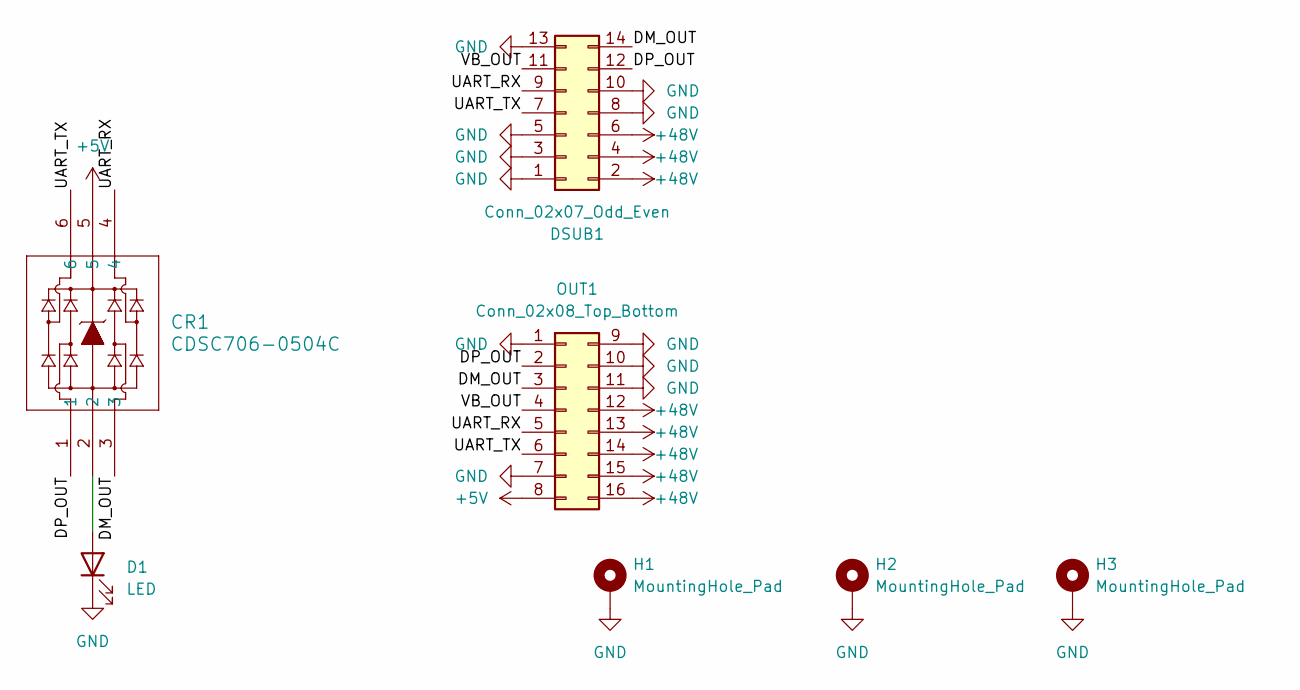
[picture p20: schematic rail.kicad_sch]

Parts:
CR1: CDSC706-0504C; CDSC706-0504C_BRN
D1: LED; LED_0603_1608Metric
DSUB1: Conn_02x07_Odd_Even; PinHeader_2x07_P2.54mm_Vertical
H1, H2, H3: MountingHole_Pad; MountingHole_3.2mm_M3_DIN965_Pad_TopBottom
OUT1: Conn_02x08_Top_Bottom; 2-1761603-6_TYC

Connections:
+5V: CR1.5, OUT1.8
+48V: DSUB1.2, DSUB1.4, DSUB1.6, OUT1.12, OUT1.13, OUT1.14, OUT1.15, OUT1.16
/DM_OUT: CR1.3, DSUB1.14, OUT1.3
/DP_OUT: CR1.1, DSUB1.12, OUT1.2
/UART_RX: CR1.4, DSUB1.9, OUT1.5
/UART_TX: CR1.6, DSUB1.7, OUT1.6
/VB_OUT: DSUB1.11, OUT1.4
GND: D1.1 (K), DSUB1.1, DSUB1.3, DSUB1.5, DSUB1.8, DSUB1.10, DSUB1.13, H1.1, H2.1, H3.1, OUT1.1, OUT1.7, OUT1.9, OUT1.10, OUT1.11
unnamed: CR1.2, D1.2 (A)

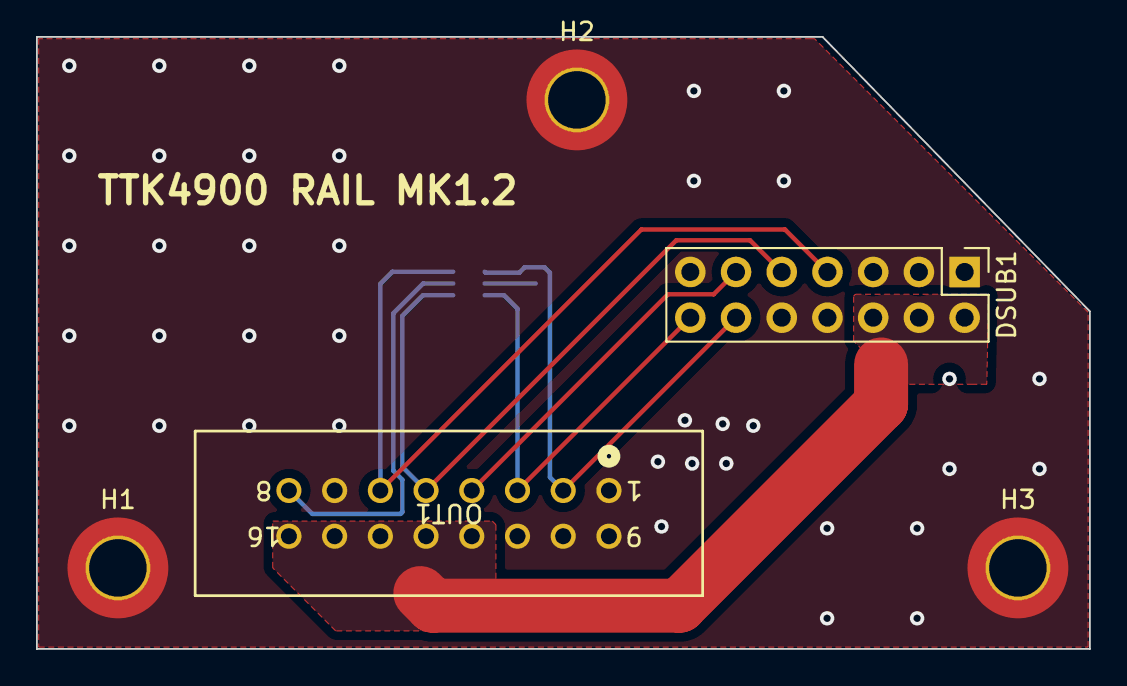
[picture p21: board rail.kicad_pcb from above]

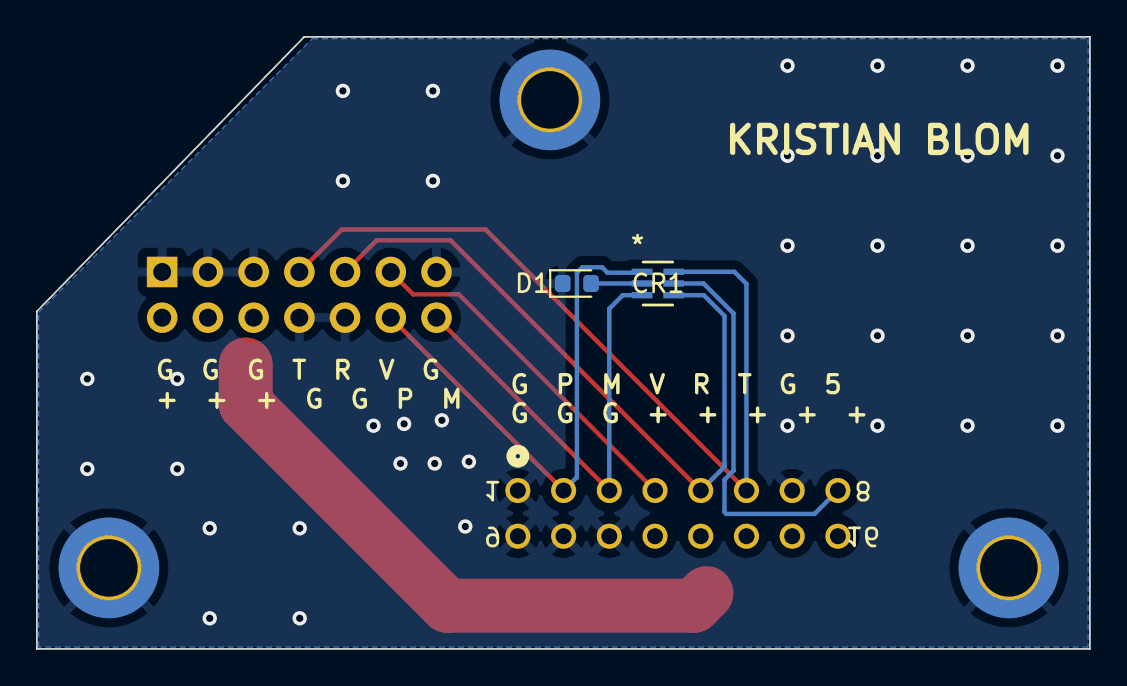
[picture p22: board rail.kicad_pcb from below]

Board: 2 copper layers, 58.5 x 34.0 mm, 7 parts (2 on the bottom side), 9 nets.

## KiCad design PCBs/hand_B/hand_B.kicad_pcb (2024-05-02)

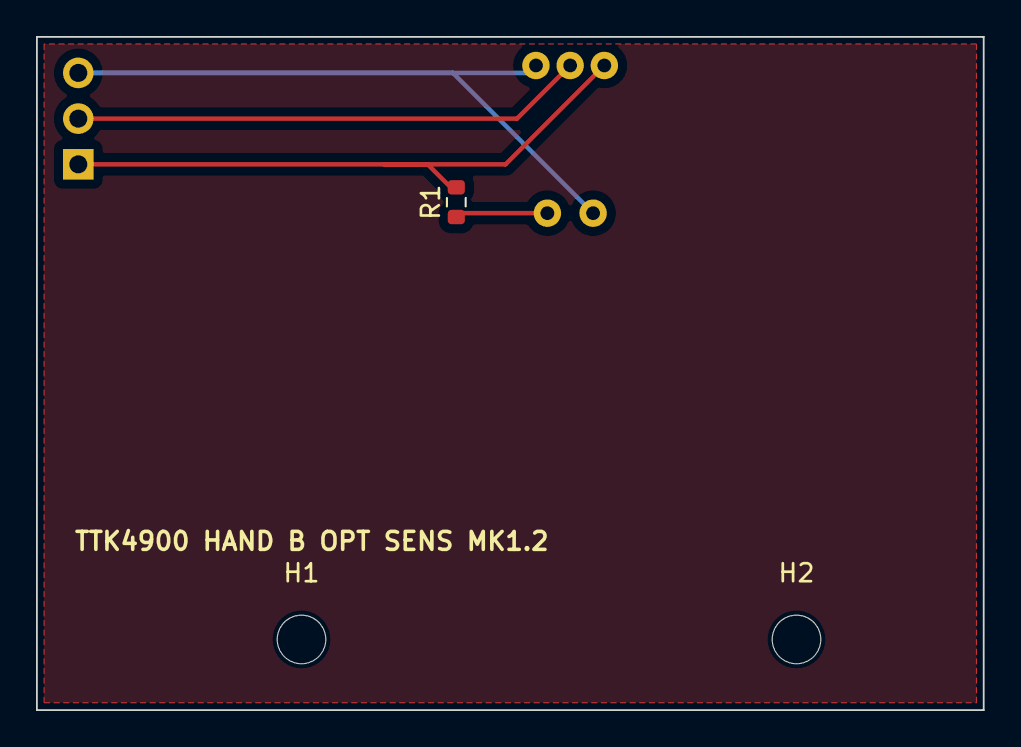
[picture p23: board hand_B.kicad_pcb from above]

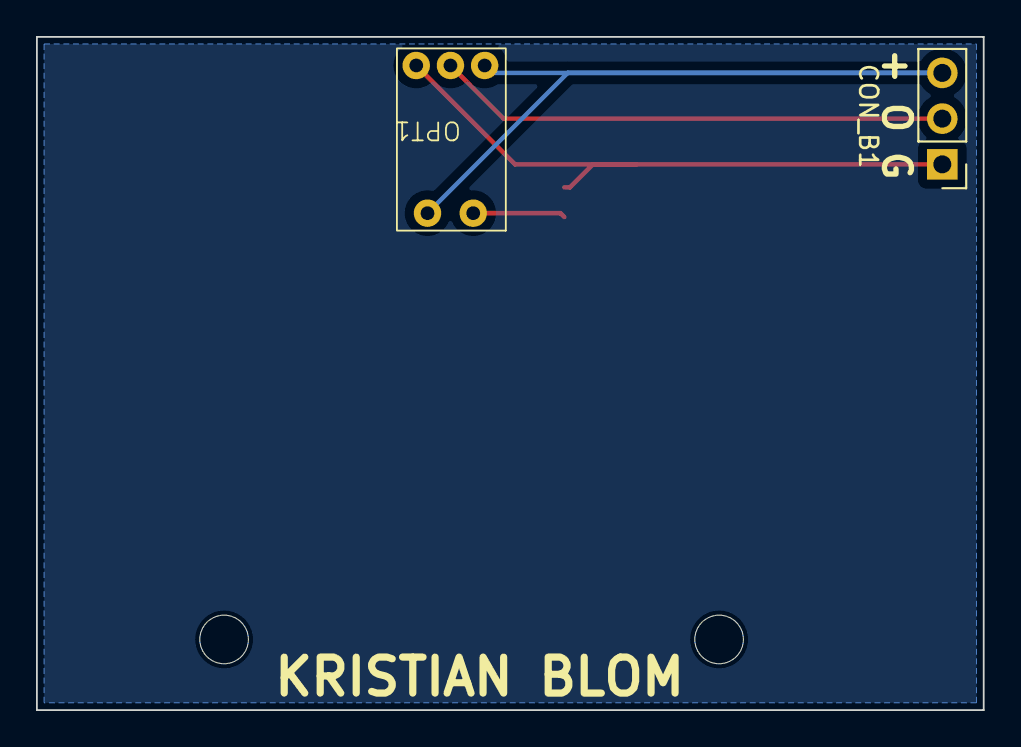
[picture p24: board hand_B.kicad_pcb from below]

Board: 2 copper layers, 52.6 x 37.4 mm, 5 parts (2 on the bottom side), 4 nets.

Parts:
CON_B1: Conn_01x03; PinHeader_1x03_P2.54mm_Vertical
H1, H2: MountingHole; MountingHole_2.7mm_M2.5
OPT1: OPB971N51
R1: 220; R_0603_1608Metric

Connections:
/0v: CON_B1.1, OPT1.5 (GND), R1.2
/5V: CON_B1.3, OPT1.1 (Anode), OPT1.3 (Vcc)
/OPT_B: CON_B1.2, OPT1.4 (Output)
unnamed: OPT1.2 (Cathode), R1.1

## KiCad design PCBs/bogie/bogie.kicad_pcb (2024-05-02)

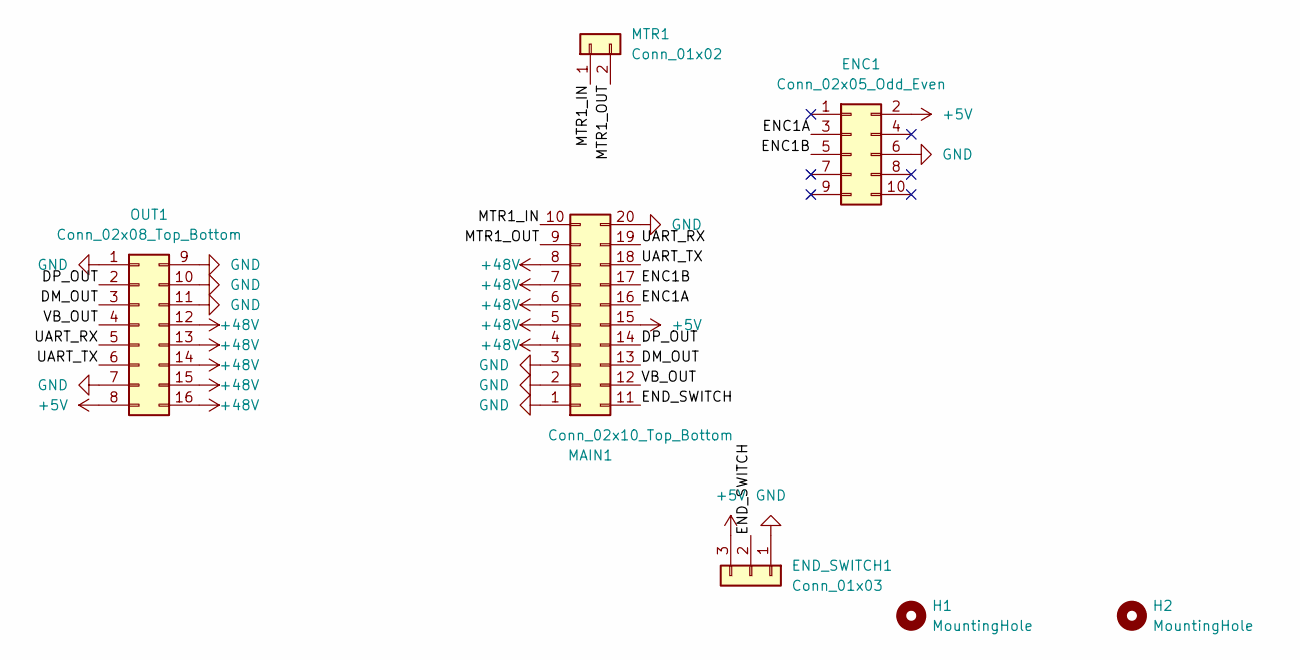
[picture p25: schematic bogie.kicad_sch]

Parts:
ENC1: Conn_02x05_Odd_Even; PinHeader_2x05_P2.54mm_Vertical
END_SWITCH1: Conn_01x03; PinHeader_1x03_P2.54mm_Vertical
H1, H2: MountingHole; MountingHole_3.7mm
MAIN1: Conn_02x10_Top_Bottom; 1761681-7_TYC
MTR1: Conn_01x02; 70543-0001_MOL
OUT1: Conn_02x08_Top_Bottom; 2-1761603-6_TYC

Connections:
+5V: ENC1.2, END_SWITCH1.3, MAIN1.15, OUT1.8
+48V: MAIN1.4, MAIN1.5, MAIN1.6, MAIN1.7, MAIN1.8, OUT1.12, OUT1.13, OUT1.14, OUT1.15, OUT1.16
/DM_OUT: MAIN1.13, OUT1.3
/DP_OUT: MAIN1.14, OUT1.2
/ENC1A: ENC1.3, MAIN1.16
/ENC1B: ENC1.5, MAIN1.17
/END_SWITCH: END_SWITCH1.2, MAIN1.11
/MTR1_IN: MAIN1.10, MTR1.1
/MTR1_OUT: MAIN1.9, MTR1.2
/UART_RX: MAIN1.19, OUT1.5
/UART_TX: MAIN1.18, OUT1.6
/VB_OUT: MAIN1.12, OUT1.4
GND: ENC1.6, END_SWITCH1.1, MAIN1.1, MAIN1.2, MAIN1.3, MAIN1.20, OUT1.1, OUT1.7, OUT1.9, OUT1.10, OUT1.11

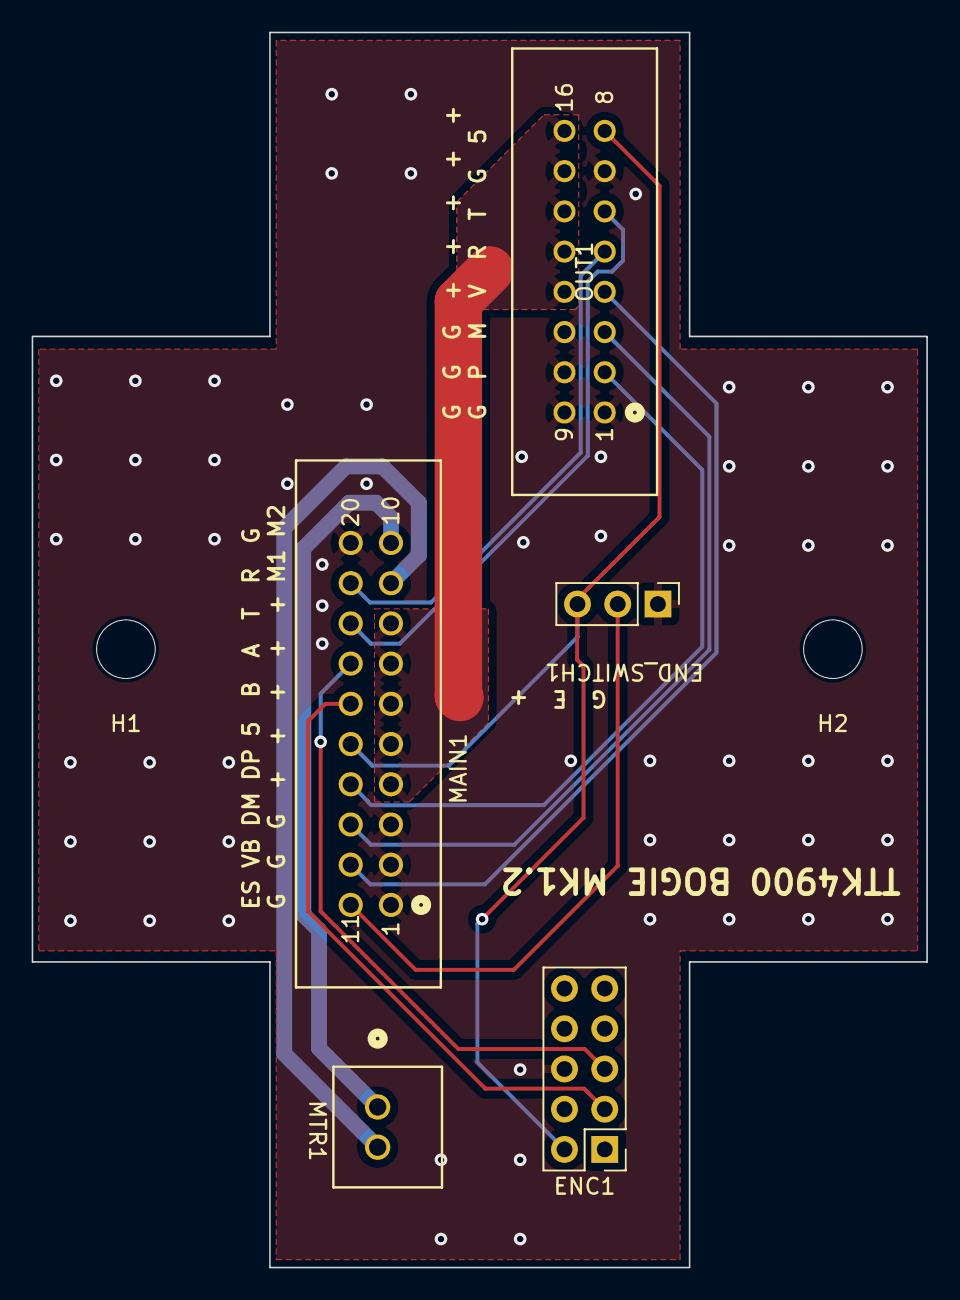
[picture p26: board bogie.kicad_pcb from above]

Board: 2 copper layers, 56.5 x 78.0 mm, 7 parts (0 on the bottom side), 13 nets.

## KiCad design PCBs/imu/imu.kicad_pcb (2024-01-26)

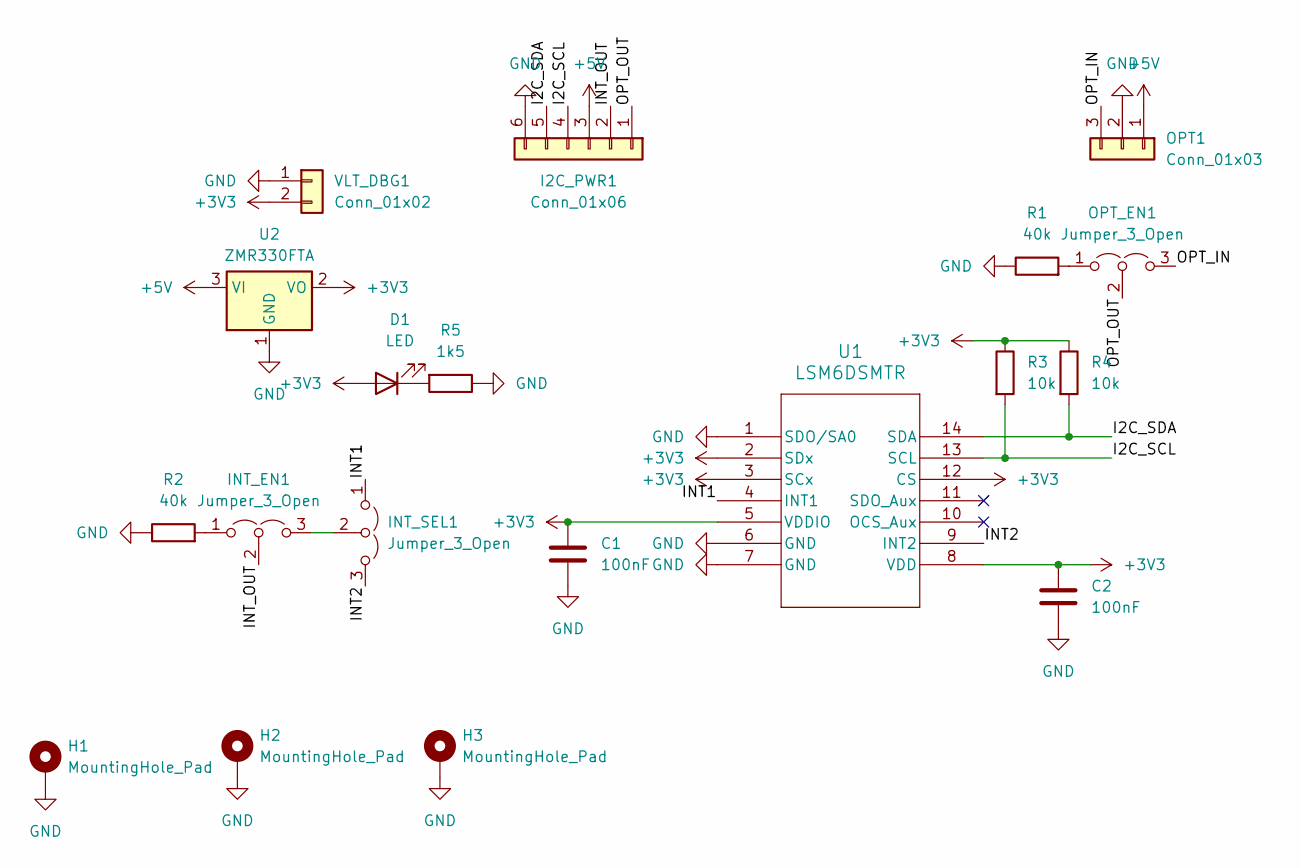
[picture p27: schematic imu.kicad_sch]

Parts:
C1, C2: 100nF; C_0603_1608Metric
D1: LED; LED_0603_1608Metric
H1, H2, H3: MountingHole_Pad; MountingHole_3.2mm_M3_DIN965_Pad_TopBottom
I2C_PWR1: Conn_01x06; PinHeader_1x06_P2.54mm_Vertical
INT_EN1: Jumper_3_Open; PinHeader_1x03_P2.54mm_Vertical
INT_SEL1: Jumper_3_Open; PinHeader_1x03_P2.54mm_Vertical
OPT1: Conn_01x03; PinHeader_1x03_P2.54mm_Vertical
OPT_EN1: Jumper_3_Open; PinHeader_1x03_P2.54mm_Vertical
R1, R2: 40k; R_0805_2012Metric
R3, R4: 10k; R_0805_2012Metric
R5: 1k5; R_0805_2012Metric
U1: LSM6DSMTR; LGA-14L_2P5X3X0P83_STM
U2: ZMR330FTA; SOT-23-3
VLT_DBG1: Conn_01x02; PinHeader_1x02_P2.54mm_Vertical

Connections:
+3V3: C1.2, C2.2, D1.2 (A), R3.1, R4.1, U1.2 (SDx), U1.3 (SCx), U1.5 (VDDIO), U1.8 (VDD), U1.12 (CS), U2.2 (VO), VLT_DBG1.2
+5V: I2C_PWR1.3, OPT1.1, U2.3 (VI)
/I2C_SCL: I2C_PWR1.4, R3.2, U1.13 (SCL)
/I2C_SDA: I2C_PWR1.5, R4.2, U1.14 (SDA)
/INT1: INT_SEL1.1 (A), U1.4 (INT1)
/INT2: INT_SEL1.3 (B), U1.9 (INT2)
/INT_OUT: I2C_PWR1.2, INT_EN1.2 (C)
/OPT_IN: OPT1.3, OPT_EN1.3 (B)
/OPT_OUT: I2C_PWR1.1, OPT_EN1.2 (C)
GND: C1.1, C2.1, H1.1, H2.1, H3.1, I2C_PWR1.6, OPT1.2, R1.1, R2.1, R5.1, U1.1 (SDO/SA0), U1.6 (GND), U1.7 (GND), U2.1 (GND), VLT_DBG1.1
unnamed: D1.1 (K), R5.2
unnamed: INT_EN1.1 (A), R2.2
unnamed: INT_EN1.3 (B), INT_SEL1.2 (C)
unnamed: OPT_EN1.1 (A), R1.2

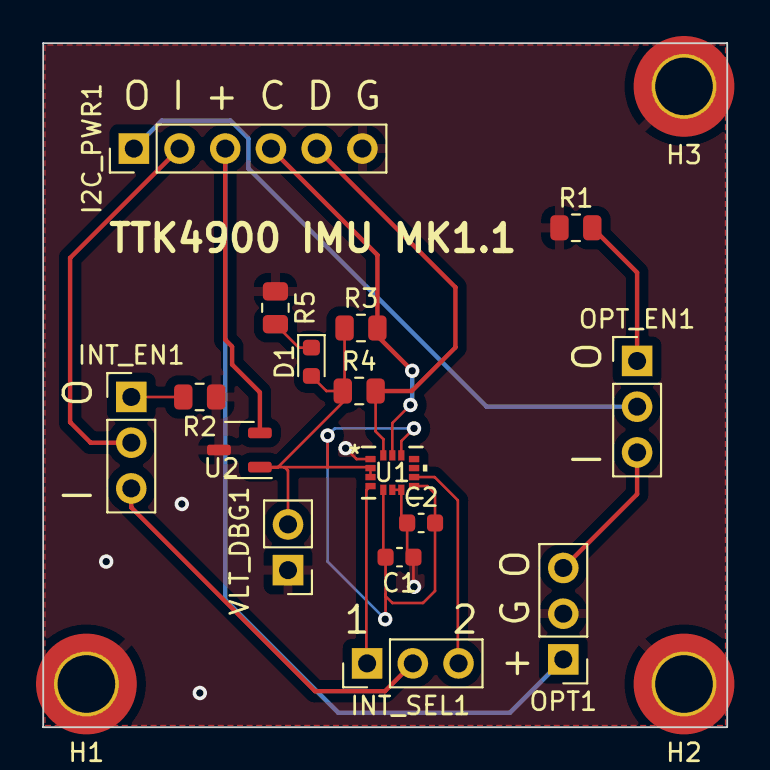
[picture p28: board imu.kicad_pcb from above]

Board: 2 copper layers, 38.0 x 38.0 mm, 19 parts (0 on the bottom side), 14 nets.

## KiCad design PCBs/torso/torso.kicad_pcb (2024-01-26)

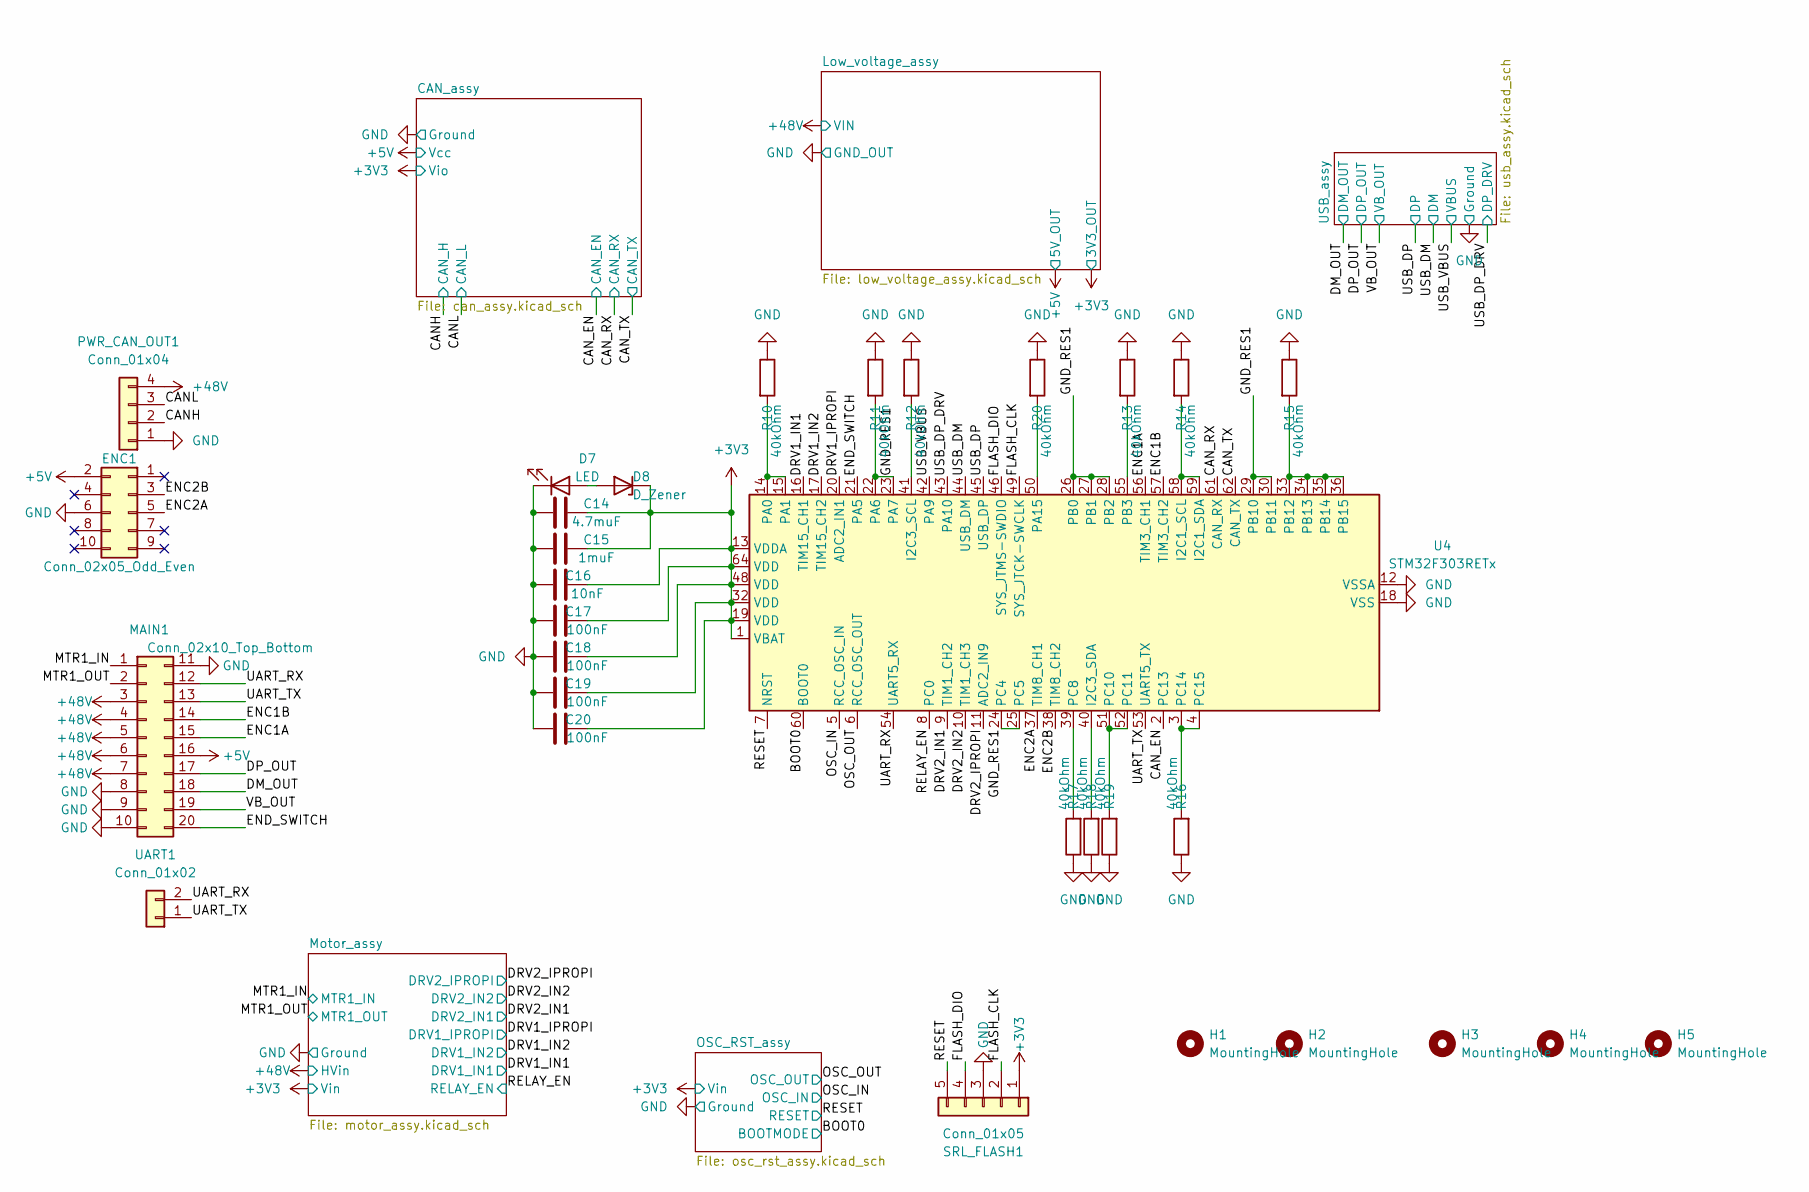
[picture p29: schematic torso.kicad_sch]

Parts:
C14: 4.7muF; C_0603_1608Metric
C15: 1muF; C_0603_1608Metric
C16: 10nF; C_0603_1608Metric
C17, C18, C19, C20: 100nF; C_0603_1608Metric
D7: LED; LED_0603_1608Metric
D8: D_Zener; D_T-1_P5.08mm_Horizontal
ENC1: Conn_02x05_Odd_Even; PinHeader_2x05_P2.54mm_Vertical
H1, H2: MountingHole; MountingHole_3.5mm
H3, H4, H5: MountingHole; MountingHole_5.3mm_M5
MAIN1: Conn_02x10_Top_Bottom; 1761681-7_TYC
PWR_CAN_OUT1: Conn_01x04; TerminalBlock_4Ucon_1x04_P3.50mm_Vertical
R10, R11, R12, R13, R14, R15, R16, R17, R18, R19, R20: 40kOhm; R_0402_1005Metric
SRL_FLASH1: Conn_01x05; PinHeader_1x05_P2.54mm_Vertical
U4: STM32F303RETx; LQFP-64_10x10mm_P0.5mm
UART1: Conn_01x02; PinHeader_1x02_P2.54mm_Vertical

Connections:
+3V3: C14.1, C15.1, C16.2, C17.2, C18.2, C19.2, C20.2, D8.1 (K), SRL_FLASH1.1, U4.1 (VBAT), U4.13 (VDDA), U4.19 (VDD), U4.32 (VDD), U4.48 (VDD), U4.64 (VDD); also elsewhere on the board
+5V: ENC1.2, MAIN1.16; also elsewhere on the board
+48V: MAIN1.3, MAIN1.4, MAIN1.5, MAIN1.6, MAIN1.7, PWR_CAN_OUT1.4 (48V); also elsewhere on the board
/BOOT0: U4.60 (BOOT0); also elsewhere on the board
/CANH: PWR_CAN_OUT1.2 (CANH); also elsewhere on the board
/CANL: PWR_CAN_OUT1.3 (CANL); also elsewhere on the board
/CAN_EN: U4.2 (PC13); also elsewhere on the board
/CAN_RX: U4.61 (CAN_RX); also elsewhere on the board
/CAN_TX: U4.62 (CAN_TX); also elsewhere on the board
/DM_OUT: MAIN1.18; also elsewhere on the board
/DP_OUT: MAIN1.17; also elsewhere on the board
/DRV1_IN1: U4.16 (TIM15_CH1); also elsewhere on the board
/DRV1_IN2: U4.17 (TIM15_CH2); also elsewhere on the board
/DRV1_IPROPI: U4.20 (ADC2_IN1); also elsewhere on the board
/DRV2_IN1: U4.9 (TIM1_CH2); also elsewhere on the board
/DRV2_IN2: U4.10 (TIM1_CH3); also elsewhere on the board
/DRV2_IPROPI: U4.11 (ADC2_IN9); also elsewhere on the board
/ENC1A: MAIN1.15, U4.56 (TIM3_CH1)
/ENC1B: MAIN1.14, U4.57 (TIM3_CH2)
/ENC2A: ENC1.5, U4.37 (TIM8_CH1)
/ENC2B: ENC1.3, U4.38 (TIM8_CH2)
/END_SWITCH: MAIN1.20, U4.21 (PA5)
/FLASH_CLK: SRL_FLASH1.2, U4.49 (SYS_JTCK-SWCLK)
/FLASH_DIO: SRL_FLASH1.4, U4.46 (SYS_JTMS-SWDIO)
/GND_RES1: R11.2, U4.22 (PA6), U4.23 (PA7), U4.24 (PC4), U4.25 (PC5), U4.26 (PB0), U4.27 (PB1), U4.28 (PB2), U4.29 (PB10), U4.30 (PB11)
/MTR1_IN: MAIN1.1; also elsewhere on the board
/MTR1_OUT: MAIN1.2; also elsewhere on the board
/OSC_IN: U4.5 (RCC_OSC_IN); also elsewhere on the board
/OSC_OUT: U4.6 (RCC_OSC_OUT); also elsewhere on the board
/RELAY_EN: U4.8 (PC0); also elsewhere on the board
/RESET: SRL_FLASH1.5, U4.7 (NRST); also elsewhere on the board
/UART_RX: MAIN1.12, U4.54 (UART5_RX), UART1.2
/UART_TX: MAIN1.13, U4.53 (UART5_TX), UART1.1
/USB_DM: U4.44 (USB_DM); also elsewhere on the board
/USB_DP: U4.45 (USB_DP); also elsewhere on the board
/USB_DP_DRV: U4.43 (PA10); also elsewhere on the board
/USB_VBUS: U4.42 (PA9); also elsewhere on the board
/VB_OUT: MAIN1.19; also elsewhere on the board
GND: C14.2, C15.2, C16.1, C17.1, C18.1, C19.1, C20.1, D7.1 (K), ENC1.6, MAIN1.8, MAIN1.9, MAIN1.10, MAIN1.11, PWR_CAN_OUT1.1 (GND), R10.1, R11.1, R12.1, R13.1, R14.1, R15.1, R16.1, R17.1, R18.1, R19.1, R20.1, SRL_FLASH1.3, U4.12 (VSSA), U4.18 (VSS), U4.31 (VSS), U4.47 (VSS), U4.63 (VSS); also elsewhere on the board
unnamed: D7.2 (A), D8.2 (A)
unnamed: R10.2, U4.14 (PA0), U4.15 (PA1)
unnamed: R12.2, U4.41 (I2C3_SCL)
unnamed: R20.2, U4.50 (PA15)
unnamed: R13.2, U4.55 (PB3)
unnamed: R14.2, U4.58 (I2C1_SCL), U4.59 (I2C1_SDA)
unnamed: R15.2, U4.33 (PB12), U4.34 (PB13), U4.35 (PB14), U4.36 (PB15)
unnamed: R17.2, U4.39 (PC8)
unnamed: R18.2, U4.40 (I2C3_SDA)
unnamed: R19.2, U4.51 (PC10), U4.52 (PC11)
unnamed: R16.2, U4.3 (PC14), U4.4 (PC15)

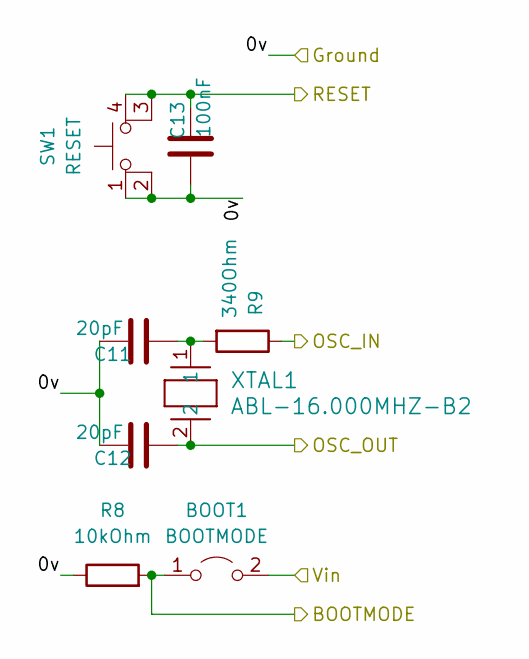
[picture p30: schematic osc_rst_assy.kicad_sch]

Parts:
BOOT1: BOOTMODE; PinHeader_1x02_P2.54mm_Vertical
C11, C12: 20pF; C_0603_1608Metric
C13: 100nF; C_0603_1608Metric
R8: 10kOhm; R_0805_2012Metric
R9: 340Ohm; R_0805_2012Metric
SW1: RESET; SW_Push_1P1T_NO_CK_KSC6xxJ
XTAL1: ABL-16.000MHZ-B2; XTAL_ABL-16_ABR

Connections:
+3V3: BOOT1.2 (B); also elsewhere on the board
/BOOT0: BOOT1.1 (A), R8.2; also elsewhere on the board
/OSC_IN: R9.1; also elsewhere on the board
/OSC_OUT: C12.1, XTAL1.2; also elsewhere on the board
/RESET: C13.2, SW1.3 (K), SW1.4 (A); also elsewhere on the board
GND: C11.2, C12.2, C13.1, R8.1, SW1.1, SW1.2; also elsewhere on the board
unnamed: C11.1, R9.2, XTAL1.1

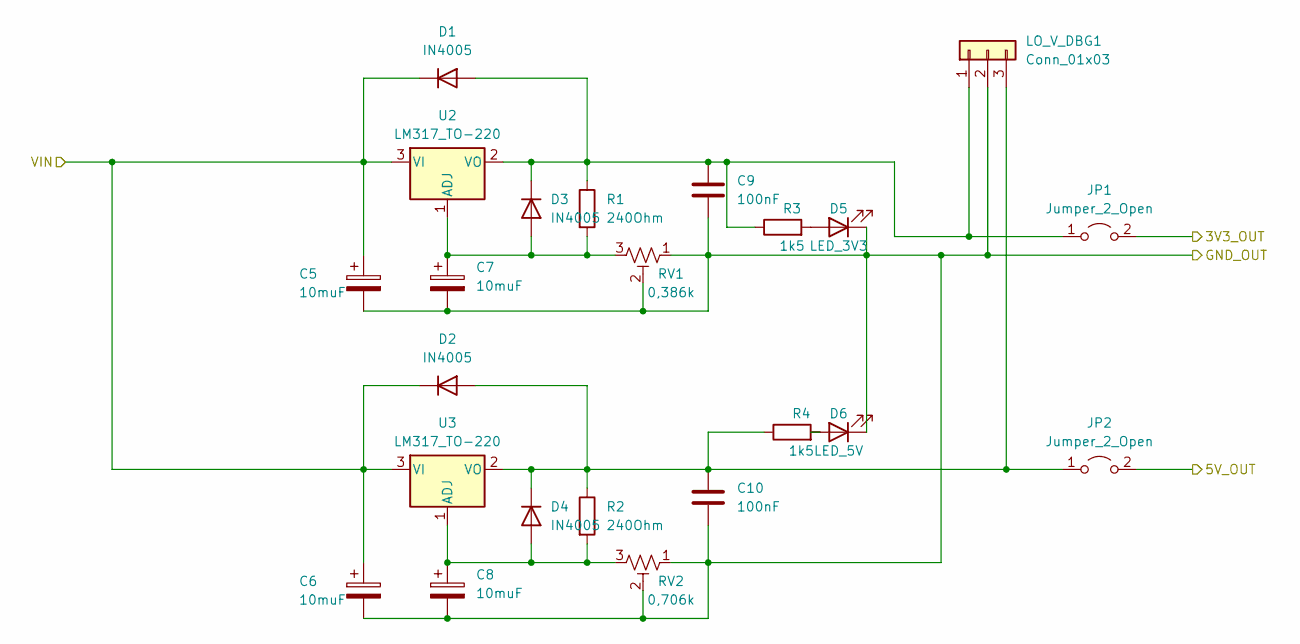
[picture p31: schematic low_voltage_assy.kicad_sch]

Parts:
C5, C6, C7, C8: 10muF; CP_Radial_D5.0mm_P2.00mm
C9, C10: 100nF; C_0603_1608Metric
D1, D2, D3, D4: IN4005; D_T-1_P5.08mm_Horizontal
D5: LED_3V3; LED_0603_1608Metric
D6: LED_5V; LED_0603_1608Metric
JP1, JP2: Jumper_2_Open; PinHeader_1x02_P2.54mm_Vertical
LO_V_DBG1: Conn_01x03; PinHeader_1x03_P2.54mm_Vertical
R1, R2: 240Ohm; R_0805_2012Metric
R3, R4: 1k5; R_0805_2012Metric
RV1: 0,386k; Potentiometer_Bourns_3006P_Horizontal
RV2: 0,706k; Potentiometer_Bourns_3006P_Horizontal
U2, U3: LM317_TO-220; TO-220-3_Horizontal_TabDown

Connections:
+3V3: JP1.2 (B); also elsewhere on the board
+5V: JP2.2 (B); also elsewhere on the board
+48V: C5.1, C6.1, D1.1 (K), D2.1 (K), U2.3 (VI), U3.3 (VI); also elsewhere on the board
GND: C5.2, C6.2, C7.2, C8.2, C9.2, C10.2, D5.1 (K), D6.1 (K), LO_V_DBG1.2, RV1.1, RV1.2, RV2.1, RV2.2; also elsewhere on the board
unnamed: C9.1, D1.2 (A), D3.1 (K), JP1.1 (A), LO_V_DBG1.1, R1.1, R3.1, U2.2 (VO)
unnamed: C10.1, D2.2 (A), D4.1 (K), JP2.1 (A), LO_V_DBG1.3, R2.1, R4.1, U3.2 (VO)
unnamed: C7.1, D3.2 (A), R1.2, RV1.3, U2.1 (ADJ)
unnamed: C8.1, D4.2 (A), R2.2, RV2.3, U3.1 (ADJ)
unnamed: D5.2 (A), R3.2
unnamed: D6.2 (A), R4.2


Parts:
CR1: USBLC6-2P6; SOT-666_STM
J3: USB_B_Micro; USB_Micro-B_Molex-105017-0001
R5: 82k; R_0603_1608Metric_Pad0.98x0.95mm_HandSolder
R6: 1k5; R_0603_1608Metric_Pad0.98x0.95mm_HandSolder
R7: 33k; R_0603_1608Metric_Pad0.98x0.95mm_HandSolder

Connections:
/DM_OUT: CR1.1 (I/O1), J3.2 (D-); also elsewhere on the board
/DP_OUT: CR1.3 (I/O2), J3.3 (D+); also elsewhere on the board
/USB_DM: CR1.6 (I/O1); also elsewhere on the board
/USB_DP: CR1.4 (I/O2), R6.1; also elsewhere on the board
/USB_DP_DRV: R6.2; also elsewhere on the board
/USB_VBUS: R5.2, R7.1; also elsewhere on the board
/VB_OUT: CR1.5 (VBUS), J3.1 (VBUS), R5.1; also elsewhere on the board
GND: CR1.2 (GND), J3.4 (ID), J3.5 (GND), J3.6 (Shield), R7.2; also elsewhere on the board


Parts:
C1, C2: 100nF; C_0603_1608Metric
CAN_TRM1: 120Ohm; R_0603_1608Metric
U1: TJA1057GT/3J; SOT96-1_SO8_NXP

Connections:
+3V3: C1.1, U1.5 (VIO); also elsewhere on the board
+5V: C2.1, U1.3 (VCC); also elsewhere on the board
/CANH: CAN_TRM1.2, U1.7 (CANH); also elsewhere on the board
/CANL: CAN_TRM1.1, U1.6 (CANL); also elsewhere on the board
/CAN_EN: U1.8 (S); also elsewhere on the board
/CAN_RX: U1.4 (RXD); also elsewhere on the board
/CAN_TX: U1.1 (TXD); also elsewhere on the board
GND: C1.2, C2.2, U1.2 (GND); also elsewhere on the board


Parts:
C3, C4: 100nF; C_0603_1608Metric
C_MTR1, C_MTR2: 330uF; CP_Radial_D16.0mm_P7.50mm
JV-3S-KT1: RELAY; JV-3S-KT
MTR2: 705430001; 70543-0001_MOL
MTR_ASY_DBG1: Conn_01x07; PinHeader_1x07_P2.54mm_Vertical
MTR_DRV1, MTR_DRV2: DRV8251ADDAR; SOIC8_DDA_TEX
Q1_RLY_CTRL1: Q_NIGBT_CGE; TO-92
RLY_CTL_DBG1: Conn_01x03; PinHeader_1x03_P2.54mm_Vertical
R_IPROPI1, R_IPROPI2: 510Ohm; R_0805_2012Metric

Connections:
+3V3: MTR_DRV1.4 (VREF), MTR_DRV2.4 (VREF), Q1_RLY_CTRL1.1 (C); also elsewhere on the board
+48V: JV-3S-KT1.3 (NO); also elsewhere on the board
/DRV1_IN1: MTR_ASY_DBG1.5, MTR_DRV1.3 (IN1); also elsewhere on the board
/DRV1_IN2: MTR_ASY_DBG1.6, MTR_DRV1.2 (IN2); also elsewhere on the board
/DRV1_IPROPI: MTR_ASY_DBG1.7, MTR_DRV1.1 (IPROPI), R_IPROPI1.1; also elsewhere on the board
/DRV2_IN1: MTR_ASY_DBG1.1, MTR_DRV2.3 (IN1); also elsewhere on the board
/DRV2_IN2: MTR_ASY_DBG1.2, MTR_DRV2.2 (IN2); also elsewhere on the board
/DRV2_IPROPI: MTR_ASY_DBG1.3, MTR_DRV2.1 (IPROPI), R_IPROPI2.1; also elsewhere on the board
/MTR1_IN: MTR_DRV1.8 (OUT2); also elsewhere on the board
/MTR1_OUT: MTR_DRV1.6 (OUT1); also elsewhere on the board
/RELAY_EN: Q1_RLY_CTRL1.2 (G), RLY_CTL_DBG1.3; also elsewhere on the board
GND: C3.1, C4.1, C_MTR1.2, C_MTR2.2, JV-3S-KT1.4, MTR_ASY_DBG1.4, MTR_DRV1.7 (GND), MTR_DRV1.9 (EPAD), MTR_DRV2.7 (GND), MTR_DRV2.9 (EPAD), RLY_CTL_DBG1.2, R_IPROPI1.2, R_IPROPI2.2; also elsewhere on the board
unnamed: C3.2, C4.2, C_MTR1.1, C_MTR2.1, JV-3S-KT1.2 (COM), MTR_DRV1.5 (VM), MTR_DRV2.5 (VM), RLY_CTL_DBG1.1
unnamed: MTR2.1 (IN), MTR_DRV2.8 (OUT2)
unnamed: MTR2.2 (OUT), MTR_DRV2.6 (OUT1)
unnamed: JV-3S-KT1.1, Q1_RLY_CTRL1.3 (E)



Board: 4 copper layers, 140.0 x 81.0 mm, 84 parts (5 on the bottom side), 61 nets.

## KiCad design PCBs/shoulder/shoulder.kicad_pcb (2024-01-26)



Board: 4 copper layers, 88.0 x 88.0 mm, 89 parts (5 on the bottom side), 63 nets.

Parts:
BOOT1: BOOTMODE; PinHeader_1x02_P2.54mm_Vertical
C1, C2, C3, C4, C5, C8, C9, C14, C15, C19, C20, C21, C22: 100nF; C_0603_1608Metric
C6, C7: 20pF; C_0603_1608Metric
C10, C11, C12, C13: 10muF; CP_Radial_D5.0mm_P2.00mm
C16: 4.7muF; C_0603_1608Metric
C17: 1muF; C_0603_1608Metric
C18: 10nF; C_0603_1608Metric
CAN_TRM1: 120Ohm; R_0603_1608Metric
CR1: USBLC6-2P6; SOT-666_STM
C_MTR1: 330muF; CP_Radial_D16.0mm_P7.50mm
C_MTR2: 220muF; CP_Radial_D10.0mm_P5.00mm
D1, D2, D3, D4: IN4005; D_T-1_P5.08mm_Horizontal
D5: LED_3V3; LED_0603_1608Metric
D6: LED_5V; LED_0603_1608Metric
D7: LED; LED_0603_1608Metric
D8: D_Zener; D_T-1_P5.08mm_Horizontal
ENC1, ENC2: Conn_02x05_Odd_Even; PinHeader_2x05_P2.54mm_Vertical
H1, H2, H3, H4: MountingHole; MountingHole_3.2mm_M3
J1: USB_B_Micro; USB_Micro-B_Molex-105017-0001
J2: Conn_01x07; PinHeader_1x07_P2.54mm_Vertical
J3: Conn_01x03; PinHeader_1x03_P2.54mm_Vertical
JP1, JP2: Jumper_2_Open; PinHeader_1x02_P2.54mm_Vertical
JV-3S-KT1: RELAY; JV-3S-KT
MTR1, MTR2: 705430001; 70543-0001_MOL
MTR_DRV1, MTR_DRV2: DRV8251ADDAR; SOIC8_DDA_TEX
PWR_CAN_IN1: Conn_01x04; TerminalBlock_4Ucon_1x04_P3.50mm_Vertical
PWR_CAN_OUT1: Conn_01x04; TerminalBlock_4Ucon_1x04_P3.50mm_Vertical
Q1_RLY_CTRL1: Q_NIGBT_CGE; TO-92
R1: 82k; R_0603_1608Metric_Pad0.98x0.95mm_HandSolder
R1_IPROPI1, R2_IPROPI1: 510Ohm; R_0805_2012Metric
R2: 33k; R_0603_1608Metric_Pad0.98x0.95mm_HandSolder
R3: 1k5; R_0603_1608Metric_Pad0.98x0.95mm_HandSolder
R4, R5: 10k; R_0805_2012Metric
R6: 340Ohm; R_0805_2012Metric
R7: 10kOhm; R_0805_2012Metric
R8, R9: 240Ohm; R_0805_2012Metric
R10, R11: 1k5; R_0805_2012Metric
R12, R13, R14, R15, R16, R17, R18, R19, R20, R21: 40kOhm; R_0402_1005Metric
RLY_CTL_DBG1: Conn_01x03; PinHeader_1x03_P2.54mm_Vertical
RV1: 0,386k; Potentiometer_Bourns_3006P_Horizontal
RV2: 0,706k; Potentiometer_Bourns_3006P_Horizontal
SRL_FLASH1: Conn_01x05; PinHeader_1x05_P2.54mm_Vertical
SW1: RESET; SW_Push_1P1T_NO_CK_KSC6xxJ
U1: STM32F303RETx; LQFP-64_10x10mm_P0.5mm
U2: LSM6DSMTR; LGA-14L_2P5X3X0P83_STM
U3: TJA1057GT/3J; SOT96-1_SO8_NXP
U4, U5: LM317_TO-220; TO-220-3_Vertical
UART1: Conn_01x02; PinHeader_1x02_P2.54mm_Vertical
XTAL1: ABL-16.000MHZ-B2; XTAL_ABL-16_ABR

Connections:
+3V3: BOOT1.2 (B), C1.1, C2.1, C8.1, C16.1, C17.1, C18.2, C19.2, C20.2, C21.2, C22.2, D8.1 (K), JP1.2 (B), MTR_DRV1.4 (VREF), MTR_DRV2.4 (VREF), Q1_RLY_CTRL1.1 (C), R4.1, R5.1, SRL_FLASH1.1, U1.1 (VBAT), U1.13 (VDDA), U1.19 (VDD), U1.32 (VDD), U1.48 (VDD), U1.64 (VDD), U2.2 (SDx), U2.3 (SCx), U2.5 (VDDIO), U2.8 (VDD), U2.12 (CS), U3.5 (VIO)
+5V: C9.1, ENC1.2, ENC2.2, JP2.2 (B), U3.3 (VCC)
+48V: C10.1, C11.1, D1.1 (K), D2.1 (K), JV-3S-KT1.3 (NO), PWR_CAN_IN1.4 (48V), PWR_CAN_OUT1.4 (48V), U4.3 (VI), U5.3 (VI)
/BOOT0: BOOT1.1 (A), R7.2, U1.60 (BOOT0)
/CANH: CAN_TRM1.2, PWR_CAN_IN1.2 (CANH), PWR_CAN_OUT1.2 (CANH), U3.7 (CANH)
/CANL: CAN_TRM1.1, PWR_CAN_IN1.3 (CANL), PWR_CAN_OUT1.3 (CANL), U3.6 (CANL)
/CAN_EN: U1.2 (PC13), U3.8 (S)
/CAN_RX: U1.61 (CAN_RX), U3.4 (RXD)
/CAN_TX: U1.62 (CAN_TX), U3.1 (TXD)
/DRV1_IN1: J2.5, MTR_DRV1.3 (IN1), U1.16 (TIM15_CH1)
/DRV1_IN2: J2.6, MTR_DRV1.2 (IN2), U1.17 (TIM15_CH2)
/DRV1_IPROPI: J2.7, MTR_DRV1.1 (IPROPI), R1_IPROPI1.1, U1.20 (ADC2_IN1)
/DRV2_IN1: J2.1, MTR_DRV2.3 (IN1), U1.9 (TIM1_CH2)
/DRV2_IN2: J2.2, MTR_DRV2.2 (IN2), U1.10 (TIM1_CH3)
/DRV2_IPROPI: J2.3, MTR_DRV2.1 (IPROPI), R2_IPROPI1.1, U1.11 (ADC2_IN9)
/ENC1A: ENC1.5, U1.56 (TIM3_CH1)
/ENC1B: ENC1.3, U1.57 (TIM3_CH2)
/ENC2A: ENC2.5, U1.38 (TIM8_CH2)
/ENC2B: ENC2.3, U1.37 (TIM8_CH1)
/FLASH_CLK: SRL_FLASH1.2, U1.49 (SYS_JTCK-SWCLK)
/FLASH_DIO: SRL_FLASH1.4, U1.46 (SYS_JTMS-SWDIO)
/GND_RES1: R13.2, U1.21 (PA5), U1.22 (PA6), U1.23 (PA7), U1.24 (PC4), U1.25 (PC5), U1.26 (PB0), U1.27 (PB1), U1.28 (PB2), U1.29 (PB10), U1.30 (PB11)
/I2C_SCL: R5.2, U1.41 (I2C3_SCL), U2.13 (SCL)
/I2C_SDA: R4.2, U1.40 (I2C3_SDA), U2.14 (SDA)
/IMU_IN2: U1.33 (PB12), U2.9 (INT2)
/IMU_INT1: U1.34 (PB13), U2.4 (INT1)
/OSC_IN: R6.1, U1.5 (RCC_OSC_IN)
/OSC_OUT: C7.1, U1.6 (RCC_OSC_OUT), XTAL1.2
/RELAY_EN: Q1_RLY_CTRL1.2 (G), RLY_CTL_DBG1.3, U1.8 (PC0)
/RESET: C5.2, SRL_FLASH1.5, SW1.3 (K), SW1.4 (A), U1.7 (NRST)
/UART_RX: U1.54 (UART5_RX), UART1.2
/UART_TX: U1.53 (UART5_TX), UART1.1
/USB_DM: CR1.6 (I/O1), U1.44 (USB_DM)
/USB_DP: CR1.4 (I/O2), R3.1, U1.45 (USB_DP)
/USB_DP_DRV: R3.2, U1.43 (PA10)
/USB_VBUS: R1.2, R2.1, U1.42 (PA9)
GND: C1.2, C2.2, C3.1, C4.1, C5.1, C6.2, C7.2, C8.2, C9.2, C10.2, C11.2, C12.2, C13.2, C14.2, C15.2, C16.2, C17.2, C18.1, C19.1, C20.1, C21.1, C22.1, CR1.2 (GND), C_MTR1.1, C_MTR2.1, D5.1 (K), D6.1 (K), D7.1 (K), ENC1.6, ENC2.6, J1.4 (ID), J1.5 (GND), J1.6 (Shield), J2.4, J3.2, JV-3S-KT1.4, MTR_DRV1.7 (GND), MTR_DRV1.9 (EPAD), MTR_DRV2.7 (GND), MTR_DRV2.9 (EPAD), PWR_CAN_IN1.1 (GND), PWR_CAN_OUT1.1 (GND), R1_IPROPI1.2, R2.2, R2_IPROPI1.2, R7.1, R12.1, R13.1, R14.1, R15.1, R16.1, R17.1, R18.1, R19.1, R20.1, R21.1, RLY_CTL_DBG1.2, RV1.1, RV1.2, RV2.1, RV2.2, SRL_FLASH1.3, SW1.1, SW1.2, U1.12 (VSSA), U1.18 (VSS), U1.31 (VSS), U1.47 (VSS), U1.63 (VSS), U2.1 (SDO/SA0), U2.6 (GND), U2.7 (GND), U3.2 (GND)
unnamed: C6.1, R6.2, XTAL1.1
unnamed: CR1.5 (VBUS), J1.1 (VBUS), R1.1
unnamed: C14.1, D1.2 (A), D3.1 (K), J3.1, JP1.1 (A), R8.1, R10.1, U4.2 (VO)
unnamed: C15.1, D2.2 (A), D4.1 (K), J3.3, JP2.1 (A), R9.1, R11.1, U5.2 (VO)
unnamed: C12.1, D3.2 (A), R8.2, RV1.3, U4.1 (ADJ)
unnamed: C13.1, D4.2 (A), R9.2, RV2.3, U5.1 (ADJ)
unnamed: D5.2 (A), R10.2
unnamed: D6.2 (A), R11.2
unnamed: D7.2 (A), D8.2 (A)
unnamed: CR1.3 (I/O2), J1.3 (D+)
unnamed: CR1.1 (I/O1), J1.2 (D-)
unnamed: C3.2, C4.2, C_MTR1.2, C_MTR2.2, JV-3S-KT1.2 (COM), MTR_DRV1.5 (VM), MTR_DRV2.5 (VM), RLY_CTL_DBG1.1
unnamed: MTR1.1 (IN), MTR_DRV1.8 (OUT2)
unnamed: MTR1.2 (OUT), MTR_DRV1.6 (OUT1)
unnamed: MTR2.1 (IN), MTR_DRV2.8 (OUT2)
unnamed: MTR2.2 (OUT), MTR_DRV2.6 (OUT1)
unnamed: JV-3S-KT1.1, Q1_RLY_CTRL1.3 (E)
unnamed: R12.2, U1.14 (PA0), U1.15 (PA1)
unnamed: R14.2, U1.50 (PA15)
unnamed: R16.2, U1.55 (PB3)
unnamed: R17.2, U1.58 (I2C1_SCL)
unnamed: R18.2, U1.59 (I2C1_SDA)
unnamed: R21.2, U1.35 (PB14), U1.36 (PB15)
unnamed: R15.2, U1.39 (PC8)
unnamed: R19.2, U1.51 (PC10), U1.52 (PC11)
unnamed: R20.2, U1.3 (PC14), U1.4 (PC15)

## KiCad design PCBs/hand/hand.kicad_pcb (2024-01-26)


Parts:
C4: 4.7muF; C_0603_1608Metric
C5: 1muF; C_0603_1608Metric
C6: 10nF; C_0603_1608Metric
C7, C8, C9, C10: 100nF; C_0603_1608Metric
D1: LED; LED_0603_1608Metric
D2: D_Zener; D_T-1_P5.08mm_Horizontal
ENC1, ENC2: Conn_01x05; PinSocket_1x05_P2.54mm_Vertical
H1, H2: MountingHole; MountingHole_2.2mm_M2
IMU_OPT1: Conn_01x02; PinHeader_1x02_P2.54mm_Vertical
PWR_CAN_IMU1: Conn_02x04_Odd_Even; PinHeader_2x04_P2.54mm_Vertical
R4, R5, R7, R11, R12, R13, R14: 40k; R_0402_1005Metric
SRL_FLS_URT1: Conn_02x05_Odd_Even; PinHeader_2x05_P2.54mm_Horizontal
U2: STM32F303RETx; LQFP-64_10x10mm_P0.5mm

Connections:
/BOOT0: U2.60 (BOOT0); also elsewhere on the board
/CANH: PWR_CAN_IMU1.6; also elsewhere on the board
/CANL: PWR_CAN_IMU1.4; also elsewhere on the board
/CAN_EN: U2.2 (PC13); also elsewhere on the board
/CAN_RX: U2.61 (CAN_RX); also elsewhere on the board
/CAN_TX: U2.62 (CAN_TX); also elsewhere on the board
/DRV1_IN1: U2.16 (TIM15_CH1); also elsewhere on the board
/DRV1_IN2: U2.17 (TIM15_CH2); also elsewhere on the board
/DRV1_IPROPI: U2.20 (ADC2_IN1); also elsewhere on the board
/DRV2_IN1: U2.9 (TIM1_CH2); also elsewhere on the board
/DRV2_IN2: U2.10 (TIM1_CH3); also elsewhere on the board
/DRV2_IPROPI: U2.11 (ADC2_IN9); also elsewhere on the board
/ENC1A: ENC1.5, U2.57 (TIM3_CH2)
/ENC1B: ENC1.3, U2.56 (TIM3_CH1)
/ENC2A: ENC2.5, U2.38 (TIM8_CH2)
/ENC2B: ENC2.3, U2.37 (TIM8_CH1)
/FLASH_CLK: SRL_FLS_URT1.3, U2.49 (SYS_JTCK-SWCLK)
/FLASH_DIO: SRL_FLS_URT1.7, U2.46 (SYS_JTMS-SWDIO)
/I2C1_SCL: PWR_CAN_IMU1.3, U2.58 (I2C1_SCL)
/I2C1_SDA: PWR_CAN_IMU1.5, U2.59 (I2C1_SDA)
/I2C3_SCL: U2.41 (I2C3_SCL); also elsewhere on the board
/I2C3_SDA: U2.40 (I2C3_SDA); also elsewhere on the board
/IMU_INT1: U2.34 (PB13); also elsewhere on the board
/IMU_INT2: U2.33 (PB12); also elsewhere on the board
/IMU_INT3: IMU_OPT1.1, U2.50 (PA15)
/OPT_SW1: U2.52 (PC11); also elsewhere on the board
/OPT_SW2: IMU_OPT1.2, U2.51 (PC10)
/OSC_IN: U2.5 (RCC_OSC_IN); also elsewhere on the board
/OSC_OUT: U2.6 (RCC_OSC_OUT); also elsewhere on the board
/RELAY_EN: U2.8 (PC0); also elsewhere on the board
/RESET: SRL_FLS_URT1.9, U2.7 (NRST); also elsewhere on the board
/UART_RX: SRL_FLS_URT1.4, U2.54 (UART5_RX)
/UART_TX: SRL_FLS_URT1.2, U2.53 (UART5_TX)
unnamed: D1.2 (A), D2.2 (A)
unnamed: R13.2, U2.14 (PA0), U2.15 (PA1)
unnamed: R14.2, U2.42 (PA9), U2.43 (PA10), U2.44 (USB_DM), U2.45 (USB_DP)
unnamed: R12.2, U2.55 (PB3)
unnamed: R5.2, U2.35 (PB14), U2.36 (PB15)
unnamed: R7.2, U2.39 (PC8)
unnamed: R11.2, U2.3 (PC14), U2.4 (PC15)


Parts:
CON_A1: Conn_01x03; PinHeader_1x03_P2.54mm_Vertical

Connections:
/OPT_SW1: CON_A1.2; also elsewhere on the board


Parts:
C15, C16: 10muF; CP_Axial_L10.0mm_D4.5mm_P15.00mm_Horizontal
C17, C18: 100nF; C_0603_1608Metric
D3, D4, D5, D6: IN4005; D_T-1_P5.08mm_Horizontal
D7: LED_3V3; LED_0603_1608Metric
D8: LED_5V; LED_0603_1608Metric
JP1, JP2: Jumper_2_Open; PinHeader_1x02_P2.54mm_Horizontal
R6, R8: 240Ohm; R_0805_2012Metric
R9, R10: 1k5; R_0805_2012Metric
RV1: 0,386k; Potentiometer_Bourns_3006P_Horizontal
RV2: 0,706k; Potentiometer_Bourns_3006P_Horizontal
U3, U4: LM317_TO-220; TO-220-3_Horizontal_TabDown

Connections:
unnamed: C17.1, D3.2 (A), D5.1 (K), JP1.1 (A), R6.1, R9.1, U3.2 (VO)
unnamed: C18.1, D4.2 (A), D6.1 (K), JP2.1 (A), R8.1, R10.1, U4.2 (VO)
unnamed: C15.1, D5.2 (A), R6.2, RV1.3, U3.1 (ADJ)
unnamed: C16.1, D6.2 (A), R8.2, RV2.3, U4.1 (ADJ)
unnamed: D7.2 (A), R9.2
unnamed: D8.2 (A), R10.2


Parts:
C3, C4: 100nF; C_0603_1608Metric
C_MTR1, C_MTR2, C_MTR3, C_MTR4, C_MTR5, C_MTR6: 47muF; CP_Elec_6.3x7.7
MTR1: Conn_02x04_Odd_Even; PinHeader_2x04_P2.54mm_Vertical
MTR_DRV1, MTR_DRV2: DRV8251ADDAR; SOIC8_DDA_TEX
R1_IPROPI: 40k; R_0402_1005Metric
R2_IPROPI: 510Ohm; R_0805_2012Metric

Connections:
/DRV1_IN1: MTR_DRV1.3 (IN1); also elsewhere on the board
/DRV1_IN2: MTR_DRV1.2 (IN2); also elsewhere on the board
/DRV1_IPROPI: MTR_DRV1.1 (IPROPI); also elsewhere on the board
/DRV2_IN1: MTR_DRV2.3 (IN1); also elsewhere on the board
/DRV2_IN2: MTR_DRV2.2 (IN2); also elsewhere on the board
/DRV2_IPROPI: MTR_DRV2.1 (IPROPI); also elsewhere on the board
unnamed: MTR1.2, MTR_DRV1.8 (OUT2)
unnamed: MTR1.4, MTR_DRV1.6 (OUT1)
unnamed: MTR1.6, MTR_DRV2.8 (OUT2)
unnamed: MTR1.8, MTR_DRV2.6 (OUT1)


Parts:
C1, C3: 100nF; C_0603_1608Metric
CAN_TRM1: 120Ohm; R_0603_1608Metric
U1: TJA1057GT/3J; SOT96-1_SO8_NXP

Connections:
/CANH: CAN_TRM1.2, U1.7 (CANH); also elsewhere on the board
/CANL: CAN_TRM1.1, U1.6 (CANL); also elsewhere on the board
/CAN_EN: U1.8 (S); also elsewhere on the board
/CAN_RX: U1.4 (RXD); also elsewhere on the board
/CAN_TX: U1.1 (TXD); also elsewhere on the board


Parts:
C21, C22: 100nF; C_0402_1005Metric
R35: 10k; R_0402_1005Metric
U5: LSM6DSMTR; LGA-14L_2P5X3X0P83_STM

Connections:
/I2C3_SCL: U5.13 (SCL); also elsewhere on the board
/I2C3_SDA: U5.14 (SDA); also elsewhere on the board
/IMU_INT1: U5.4 (INT1); also elsewhere on the board
/IMU_INT2: U5.9 (INT2); also elsewhere on the board


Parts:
BOOT0: BOOTMODE; PinHeader_1x02_P2.54mm_Horizontal
C2: 100nF; C_0603_1608Metric
C11, C12: 20pF; C_0603_1608Metric
J6: Conn_01x02; PinHeader_1x02_P2.54mm_Horizontal
R1: 10kOhm; R_0805_2012Metric
R4: 340Ohm; R_0805_2012Metric
XTAL1: ABL-16.000MHZ-B2; XTAL_ABL-16_ABR

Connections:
/BOOT0: R1.2; also elsewhere on the board
/OSC_OUT: C12.1, XTAL1.2; also elsewhere on the board
/RESET: J6.2; also elsewhere on the board

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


Board: 4 copper layers, 55.5 x 91.0 mm, 76 parts (12 on the bottom side), 56 nets.

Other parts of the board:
BOOT1: BOOTMODE; PinHeader_1x02_P2.54mm_Horizontal
C13, C14, C19: 100nF; C_0603_1608Metric
R3: 340Ohm; R_0805_2012Metric
R27, R31: 10k; R_0402_1005Metric
R_EN1: 40k; R_0402_1005Metric
R_IPROPI1, R_IPROPI2: 510Ohm; R_0805_2012Metric

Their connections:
/BOOT0: BOOT1.1 (A); also elsewhere on the board
/DRV1_IPROPI: R_IPROPI1.1; also elsewhere on the board
/DRV2_IPROPI: R_IPROPI2.1; also elsewhere on the board
/I2C3_SCL: R31.2; also elsewhere on the board
/I2C3_SDA: R27.2; also elsewhere on the board
/OSC_IN: R3.1; also elsewhere on the board
/RELAY_EN: R_EN1.2; also elsewhere on the board
/RESET: C19.2; also elsewhere on the board

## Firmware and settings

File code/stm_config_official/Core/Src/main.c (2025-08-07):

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
/* Includes ------------------------------------------------------------------*/
#include "main.h"
#include "adc.h"
#include "can.h"
#include "i2c.h"
#include "tim.h"
#include "usart.h"
#include "usb_device.h"
#include "gpio.h"

/* USER CODE BEGIN Includes */
#include "stm32f3xx_hal.h"
#include "stm32f3xx_hal_can.h"

#include "unit_config.h"
#include "can_driver.h"
#include "gpio_driver.h"
#include "uart_driver.h"
#include "motor_driver.h"
#include "adc_driver.h"
#include "state_machine.h"
#include "ros_uart_parser.h"
#include "string_cmd_parser.h"

#if ACTIVE_UNIT == SHOULDER
#include "accelerometer_driver.h"
#endif
/* USER CODE END Includes */


void SystemClock_Config(void);
/**
  * @brief  The application entry point.
  * @retval int
  */
int main(void)
{
  /* MCU Configuration--------------------------------------------------------*/

  /* Reset of all peripherals, Initializes the Flash interface and the Systick. */
  HAL_Init();

  /* Configure the system clock */
  SystemClock_Config();

  /* Initialize all configured peripherals */
  MX_GPIO_Init();
  MX_ADC2_Init();
  MX_CAN_Init();
  MX_TIM3_Init();
  MX_TIM8_Init();
  MX_TIM15_Init();
  MX_I2C1_Init();
  MX_UART5_Init();
  MX_I2C3_Init();
  MX_TIM1_Init();
  MX_USB_DEVICE_Init();
  MX_TIM2_Init();
  MX_ADC1_Init();
  MX_TIM4_Init();
  MX_TIM7_Init();
  /* USER CODE BEGIN 2 */
#if (HW_INTERFACE == UART_INTERFACE)  && (SW_INTERFACE == CMD_MODE_TERMINAL)  
  uart_send_string("Peripheral init complete\n\r");
#endif
  
  HAL_TIM_PWM_Start(&htim1, TIM_CHANNEL_2);//MTR2
  HAL_TIM_PWM_Start(&htim1, TIM_CHANNEL_3);//MTR2
  HAL_TIM_PWM_Start(&htim15, TIM_CHANNEL_1);//MTR1
  HAL_TIM_PWM_Start(&htim15, TIM_CHANNEL_2);//MTR1

  HAL_TIM_Encoder_Start(&htim3, TIM_CHANNEL_ALL);
  HAL_TIM_Encoder_Start(&htim8, TIM_CHANNEL_ALL);

  HAL_TIM_Base_Start_IT(&htim2);//CAN timer interrupt
  HAL_TIM_Base_Start_IT(&htim4);//Controller update timer interrupt
  HAL_TIM_Base_Start_IT(&htim7);//Telemetry (UART) timer interrupt

  HAL_CAN_Start(&hcan);
  HAL_CAN_ActivateNotification(&hcan, CAN_IT_RX_FIFO0_MSG_PENDING);

  HAL_ADC_Start(&hadc1);
  HAL_ADC_Start(&hadc2);

#if (HW_INTERFACE == UART_INTERFACE)  && (SW_INTERFACE == CMD_MODE_TERMINAL)
  uart_hmi_init();
#elif (HW_INTERFACE == UART_INTERFACE) && (SW_INTERFACE == CMD_MODE_ROS)
  uart_ros_init();
  // state_interface_set_global_state(GS_OPERATING);
  // state_interface_broadcast_global_state();
#endif

  /* USER CODE END 2 */

  /* Infinite loop */
  /* USER CODE BEGIN WHILE */
  uart_send_string("hello world\n\r");
  HAL_Delay(2000);
  HAL_GPIO_WritePin(RELAY_EN_GPIO_Port, RELAY_EN_Pin, 1);

#if ACTIVE_UNIT == SHOULDER
  accl_interface_set_byte(0x10, 0b01110000); //Init acc 2g
  accl_interface_set_byte(0x11, 0b01110000); //Init rotation 250dps
#endif

  while (1)
  {


#if (ACTIVE_UNIT == TORSO) && (SW_INTERFACE == CMD_MODE_ROS)
    if(ros_interface_get_newMsgFlag() == 1)
    {
      //uart_send_string("about to parse ros input\n\r");
      ros_interface_parse_input();
      ros_interface_clear_newMsgFlag();
    }
#endif    
    
    can_rx_executive();
    can_tx_executive();

    motor_interface_update_tot_cnt(0);
    motor_interface_update_tot_cnt(1);

    if(state_interface_get_global_state() == GS_IDLE)
    {
      //Do nothing
    }
    if(state_interface_get_global_state() == GS_CALIBRATING)
    {
#if ACTIVE_UNIT == TORSO
      if(state_interface_get_calibration_state() == CS_RAIL)
      {
        state_calibrate_rail();
        state_interface_set_calibration_state(CS_SHOULDER);
        state_interface_broadcast_calibration_state();
      }
      else if(state_interface_get_calibration_state() == CS_SHOULDER)
      {
        state_calibrate_shoulder();
        
        if(fabs(controller_interface_get_error(1)) < 0.04)
        {
          //motor_interface_zero(1);
          char debug[64];
          sprintf(debug, "\nFinal shoulder calibration error: %i\n\r", (int32_t)(controller_interface_get_error(1)*1000));
          uart_send_string(debug);          

          motor_interface_set_total_count(1, 0);
          state_interface_set_calibration_state(CS_TWIST);
          state_interface_broadcast_calibration_state();
        }
      }
#elif ACTIVE_UNIT == SHOULDER
      if(state_interface_get_calibration_state() == CS_WRIST)
      {
        HAL_Delay(1000); //Wait for the twist to stabilise
        state_calibrate_wrist();
        state_interface_set_calibration_state(CS_ELBOW);
        state_interface_broadcast_calibration_state();        
      }
      else if(state_interface_get_calibration_state() == CS_ELBOW)
      {
        state_calibrate_elbow();
        state_interface_set_calibration_state(CS_ERROR);
        state_interface_set_global_state(GS_OPERATING);
        state_interface_broadcast_global_state();
      }
#elif ACTIVE_UNIT == HAND
      if(state_interface_get_calibration_state() == CS_TWIST)
      {
        state_calibrate_twist();
        state_interface_set_calibration_state(CS_PINCH);
        state_interface_broadcast_calibration_state();
      }
      else if(state_interface_get_calibration_state() == CS_PINCH)
      {
        state_calibrate_pinch();
        state_interface_set_calibration_state(CS_WRIST);
        state_interface_broadcast_calibration_state();

      }    
#endif
      else
      {
        //If not calibrating own joints, maintain positions
        controller_interface_update_controller();
      }
    }
    else if(state_interface_get_global_state() == GS_OPERATING)
    {
      controller_interface_update_controller();
    }
    
    
#if ACTIVE_UNIT == TORSO
    if(controller_interface_get_acc_poll() == 1)
    {
      controller_interface_request_acc_axis(1, 0, 'y');
      controller_interface_clear_acc_poll();
    }

    if((controller_interface_get_upd_telemetry() == 1))
    {
      float shoulderPos = controller_interface_get_position(1);
      float shoulderSp = controller_interface_get_setpoint(1);
      float shoulderEr = controller_interface_get_error(1);


      int32_t posAsInt = (int32_t)(shoulderPos*1000);
      int32_t spAsInt = (int32_t)(shoulderSp*1000);
      int32_t erAsInt = (int32_t)(shoulderEr*1000);
      int32_t totalCount = motor_interface_get_total_count(1);


      char* telemetry[128];
      sprintf(telemetry, "%i;%i;%i\r", totalCount, spAsInt, erAsInt);
      //uart_send_string(telemetry);      
      controller_interface_clear_upd_telemetry();
    }
#endif
    
    adc_interface_update_current(0);
    adc_interface_update_current(1);
    
    /* USER CODE END WHILE */

    /* USER CODE BEGIN 3 */
  }
  /* USER CODE END 3 */
}

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


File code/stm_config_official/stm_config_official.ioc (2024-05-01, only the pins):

Mcu.UserName=STM32F303RETx
PA10.GPIO_Label=USB_DP_DRV
PA10.Signal=GPIO_Output
PA11.Signal=USB_DM
PA12.Signal=USB_DP
PA13.Signal=SYS_JTMS-SWDIO
PA14.Signal=SYS_JTCK-SWCLK
PA15.GPIO_Label=END_SW_BAK
PA15.Signal=GPXTI15
PA2.GPIO_Label=DRV1_IN1
PA2.Signal=S_TIM15_CH1
PA3.GPIO_Label=DRV1_IN2
PA3.Signal=S_TIM15_CH2
PA4.GPIO_Label=DRV1_VIP
PA4.Signal=ADC2_IN1
PA5.GPIO_Label=END_SW
PA5.Signal=GPXTI5
PA8.Signal=I2C3_SCL
PA9.GPIO_Label=USB_VB
PA9.Signal=GPXTI9
PB12.GPIO_Label=IMU_INT2
PB12.Signal=GPIO_Output
PB13.GPIO_Label=IMU_INT1
PB13.Signal=GPIO_Output
PB4.GPIO_Label=ENC1A
PB4.Signal=S_TIM3_CH1
PB5.GPIO_Label=ENC1B
PB5.Signal=S_TIM3_CH2
PB6.Signal=I2C1_SCL
PB7.Signal=I2C1_SDA
PB8.Signal=CAN_RX
PB9.Signal=CAN_TX
PC0.GPIO_Label=RELAY_EN
PC0.Signal=GPIO_Output
PC1.GPIO_Label=DRV2_IN1
PC1.Signal=S_TIM1_CH2
PC10.GPIO_Label=OPT_SW2
PC10.Signal=GPXTI10
PC11.GPIO_Label=OPT_SW1
PC11.Signal=GPXTI11
PC12.Signal=UART5_TX
PC13.GPIO_Label=CAN_EN
PC13.Signal=GPIO_Output
PC2.GPIO_Label=DRV2_IN2
PC2.Signal=S_TIM1_CH3
PC3.GPIO_Label=DRV2_VIP
PC3.Signal=ADCx_IN9
PC6.GPIO_Label=ENC2B
PC6.Signal=S_TIM8_CH1
PC7.GPIO_Label=ENC2A
PC7.Signal=S_TIM8_CH2
PC9.Signal=I2C3_SDA
PD2.Signal=UART5_RX
PF0-OSC_IN.Signal=RCC_OSC_IN
PF1-OSC_OUT.Signal=RCC_OSC_OUT

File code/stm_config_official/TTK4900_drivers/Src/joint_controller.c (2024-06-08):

#include "joint_controller.h"

#if ACTIVE_UNIT == TORSO
static joint_controller_descriptor joint0 =
{
  .hasAccelerometer = 0,
  .posSetpoint = 0,
  .posCurrent = 0,
  .posError = 0,
  .prevError = 0,
  .prevPower = 0,
  .isMoving = 0,
  .motorNum = 0,
  .sigmoidIntGain = 0,
  .Kp = 0.5, //1
  .KpTi = 0.0002,//0.0025,//0.0001,
  .Kd = 0.1,//0.08, //0.25
  .intError = 0,
  .jointName = "rail"
};

static joint_controller_descriptor joint1 =
{
  .hasAccelerometer = 0, //Was set to 0 for demonstration in public, very unsafe when activated
  .posSetpoint = 0,
  .posCurrent = 0,
  .posError = 0,
  .isMoving = 0,
  .motorNum = 1,
  .sigmoidIntGain = 1,
  .Kp = 60,
  .KpTi = 0.02,
  .Kd = 10,
  .intError = 0,  
  .jointName = "shoulder"
};

#elif ACTIVE_UNIT == SHOULDER
static joint_controller_descriptor joint0 =
{
  .hasAccelerometer = 0,
  .posSetpoint = 0,
  .posCurrent = 0,
  .posError = 0,
  .isMoving = 0,
  .motorNum = 0,
  .sigmoidIntGain = 1,
  .Kp = 50,
  .KpTi = 0.07, //0.0001,
  .Kd = 20,
  .intError = 0,
  .jointName = "wrist"
};

static joint_controller_descriptor joint1 =
{
  .hasAccelerometer = 0,
  .posSetpoint = 0,
  .posCurrent = 0,
  .posError = 0,
  .isMoving = 0,
  .motorNum = 1,
  .sigmoidIntGain = 1,
  .Kp = 50,
  .KpTi = 0.005,// 0.0003,
  .Kd = 30,
  .intError = 0,  
  .jointName = "elbow"
};

#elif ACTIVE_UNIT == HAND

static joint_controller_descriptor joint0 =
{
  .hasAccelerometer = 0,
  .posSetpoint = 0,
  .posCurrent = 0,
  .posError = 0,
  .isMoving = 0,
  .motorNum = 0,
  .sigmoidIntGain = 0,
  .Kp = 20,
  .KpTi = 0.01,//0.0001,
  .Kd = 0,
  .intError = 0,  
  .jointName = "pinch"
};

static joint_controller_descriptor joint1 =
{
  .hasAccelerometer = 0,
  .posSetpoint = 0,
  .posCurrent = 0,
  .posError = 0,
  .isMoving = 0,
  .motorNum = 1,
  .sigmoidIntGain = 1,
  .Kp = 40,
  .KpTi = 0.01,//0.0003,
  .Kd = 7,
  .intError = 0,  
  .jointName = "twist"
};
#endif

joint_controller_descriptor* joints[2] =
{
  &joint0,
  &joint1
};

/// @brief Ensures polling of accelerometers is kept below a safe maximum frequency
static uint8_t accelerometer_poll_safe = 0;

/// @brief Ensures polling of motors is kept below a safe maximum frequency
static uint8_t motor_poll_safe = 0;

/// @brief Ensures a predictable rate of PID updates
static uint8_t update_controller = 0;


static uint8_t update_telemetry = 0;

#if ACTIVE_UNIT == TORSO
//Torso uses one accelerometer: Shoulder control
accelerometer_inData accelerometers[1];
#elif ACTIVE_UNIT == SHOULDER
//Shoulder uses two accelerometers: Elbow and wrist control
accelerometer_inData* accelerometers[2];
#elif ACTIVE_UNIT == HAND
//Hand uses no accelerometers, but adding this is easier than
//selectively compiling the dependent functions
accelerometer_inData* accelerometers[0];

#endif


//Public functions

//----------------------
//Joint control handlers
//----------------------
void controller_interface_update_controller()
{
  if(controller_interface_get_upd_ctrl() == 1)
  {
    controller_interface_update_position(0);
    controller_interface_update_position(1);

    
    controller_interface_update_error(0);
    controller_interface_update_error(1);
    
    controller_interface_update_power(0);
    controller_interface_update_power(1);

    controller_interface_clear_upd_ctrl();
  }
}

float controller_interface_get_setpoint(uint8_t controllerSelect)
{
  return joint_controller_get_setpoint(joints[controllerSelect]);
}


void controller_interface_set_setpoint(uint8_t controllerSelect, float setPoint)
{
  joint_controller_set_setpoint(joints[controllerSelect], setPoint);
}


float controller_interface_get_position(uint8_t controllerSelect)
{
  return joint_controller_get_position(joints[controllerSelect]);
}

void controller_interface_update_position(uint8_t controllerSelect)
{
  joint_controller_update_position(joints[controllerSelect]);
}

void controller_interface_set_position(uint8_t controllerSelect, float position)

{
  joint_controller_set_setpoint(joints[controllerSelect], position);
}


float controller_interface_get_error(uint8_t controllerSelect)
{
  return joint_controller_get_error(joints[controllerSelect]);
}

void controller_interface_update_error(uint8_t controllerSelect)
{
  joint_controller_update_error(joints[controllerSelect]);
}

void controller_interface_set_error(uint8_t controllerSelect, float error)
{
  joint_controller_set_error(joints[controllerSelect], error);
}


uint8_t controller_interface_get_moving(uint8_t controllerSelect)
{
  return joint_controller_get_moving(joints[controllerSelect]);
}


void controller_interface_set_moving(uint8_t controllerSelect)
{
  joint_controller_set_moving(joints[controllerSelect]);
}


void controller_interface_clear_moving(uint8_t controllerSelect)
{
  joint_controller_clear_moving(joints[controllerSelect]);
}

void controller_interface_set_power(uint8_t controllerSelect, float power)
{
  joint_controller_set_power(joints[controllerSelect], power);
}

void controller_interface_update_power(uint8_t controllerSelect)
{
  joint_controller_update_power(joints[controllerSelect]);
}


float controller_interface_clicks_to_pos(uint8_t controllerSelect)
{
  return joint_controller_clicks_to_pos(joints[controllerSelect]);
}

void controller_interface_request_acc_axis(uint8_t controllerSelect, uint8_t accSelect, char axis)
{
  joint_controller_request_acc_axis(joints[controllerSelect], accSelect, axis);
}

//----------------------
//Accelerometer data handlers
//----------------------

int16_t controller_interface_acc_getX(uint8_t accSelect)
{
  return controller_acc_getX(&accelerometers[accSelect]);
}
int16_t controller_interface_acc_getY(uint8_t accSelect)
{
  return controller_acc_getY(&accelerometers[accSelect]);
}
int16_t controller_interface_acc_getZ(uint8_t accSelect)
{
  return controller_acc_getX(&accelerometers[accSelect]);
}


void controller_interface_acc_setX(uint8_t accSelect, int16_t accVal)
{
  controller_acc_setX(&accelerometers[accSelect], accVal);
}
void controller_interface_acc_setY(uint8_t accSelect, int16_t accVal)
{
  controller_acc_setY(&accelerometers[accSelect], accVal);
}
void controller_interface_acc_setZ(uint8_t accSelect, int16_t accVal)
{
  controller_acc_setZ(&accelerometers[accSelect], accVal);
}

int16_t controller_interface_rot_getX(uint8_t accSelect)
{
  return controller_rot_getX(&accelerometers[accSelect]);
}
int16_t controller_interface_rot_getY(uint8_t accSelect)
{
  return controller_rot_getY(&accelerometers[accSelect]);
}
int16_t controller_interface_rot_getZ(uint8_t accSelect)
{
  return controller_rot_getZ(&accelerometers[accSelect]);
}

void controller_interface_rot_setX(uint8_t accSelect, int16_t rotVal)
{
  controller_rot_setX(&accelerometers[accSelect], rotVal);
}
void controller_interface_rot_setY(uint8_t accSelect, int16_t rotVal)
{
  controller_rot_setY(&accelerometers[accSelect], rotVal);
}
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

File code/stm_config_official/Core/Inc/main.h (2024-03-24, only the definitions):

#define CAN_EN_Pin GPIO_PIN_13
#define CAN_EN_GPIO_Port GPIOC
#define RELAY_EN_Pin GPIO_PIN_0
#define RELAY_EN_GPIO_Port GPIOC
#define DRV2_IN1_Pin GPIO_PIN_1
#define DRV2_IN1_GPIO_Port GPIOC
#define DRV2_IN2_Pin GPIO_PIN_2
#define DRV2_IN2_GPIO_Port GPIOC
#define DRV2_VIP_Pin GPIO_PIN_3
#define DRV2_VIP_GPIO_Port GPIOC
#define DRV1_IN1_Pin GPIO_PIN_2
#define DRV1_IN1_GPIO_Port GPIOA
#define DRV1_IN2_Pin GPIO_PIN_3
#define DRV1_IN2_GPIO_Port GPIOA
#define DRV1_VIP_Pin GPIO_PIN_4
#define DRV1_VIP_GPIO_Port GPIOA
#define END_SW_Pin GPIO_PIN_5
#define END_SW_GPIO_Port GPIOA
#define END_SW_EXTI_IRQn EXTI9_5_IRQn
#define IMU_INT2_Pin GPIO_PIN_12
#define IMU_INT2_GPIO_Port GPIOB
#define IMU_INT1_Pin GPIO_PIN_13
#define IMU_INT1_GPIO_Port GPIOB
#define ENC2B_Pin GPIO_PIN_6
#define ENC2B_GPIO_Port GPIOC
#define ENC2A_Pin GPIO_PIN_7
#define ENC2A_GPIO_Port GPIOC
#define USB_VB_Pin GPIO_PIN_9
#define USB_VB_GPIO_Port GPIOA
#define USB_VB_EXTI_IRQn EXTI9_5_IRQn
#define USB_DP_DRV_Pin GPIO_PIN_10
#define USB_DP_DRV_GPIO_Port GPIOA
#define END_SW_BAK_Pin GPIO_PIN_15
#define END_SW_BAK_GPIO_Port GPIOA
#define END_SW_BAK_EXTI_IRQn EXTI15_10_IRQn
#define OPT_SW2_Pin GPIO_PIN_10
#define OPT_SW2_GPIO_Port GPIOC
#define OPT_SW2_EXTI_IRQn EXTI15_10_IRQn
#define OPT_SW1_Pin GPIO_PIN_11
#define OPT_SW1_GPIO_Port GPIOC
#define OPT_SW1_EXTI_IRQn EXTI15_10_IRQn
#define ENC1A_Pin GPIO_PIN_4
#define ENC1A_GPIO_Port GPIOB
#define ENC1B_Pin GPIO_PIN_5
#define ENC1B_GPIO_Port GPIOB

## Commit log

2024-01-17 Added ignr, folderer structure, some documentation
    [bogie.kicad_pcb, bogie.kicad_sch, hand.kicad_pcb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]
2024-01-17 Shoulder motor assy almost done. Need to find a library for the 2N551 NPN and redo the circuit. Ensure that the footprint pinout is correct
    [can_assy.kicad_sch, imu_assy.kicad_sch, low_voltage_assy.kicad_sch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]
2024-01-18 Torso schematic almost complete, missing pulldowns and a decision on the I2C header matter
2024-01-19 Torso all but complete, making bogie before checking the last mark
    [can_assy.kicad_sch, imu_assy.kicad_sch, low_voltage_assy.kicad_sch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]
2024-01-19 Torso, bogie and rail complete. Next up: revise hand and IMU board in conjunction
    [bogie.kicad_pcb, bogie.kicad_sch, rail.kicad_pcb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]
2024-01-24 Hand schematic changes complete. Found IMU dc buck, see journal. Next up: trace hand
    [BOM_hand.csv, IMU_assy.kicad_sch, Low_voltage_assy.kicad_sch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]
2024-01-25 Updated ign with ever more variations of autosaves. Finished tracing hand, probably need new footprint for encoders. Next up: find footprints, redo IMU board
    [IMU_assy.kicad_sch, hand.kicad_pcb, hand.kicad_sch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]
2024-01-26 All revisions finished, MK1.1 ready for gerber generation
    [BOM_hand.csv, hand.kicad_pcb, hand.kicad_sch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]
2024-01-26 Separated Hand B as separate Kicad project. Next up: gerber generation
    [hand.kicad_pcb, hand.kicad_sch, hand_B.kicad_pcb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]
2024-01-26 All gerbers generated. Next up: BOM
    [bogie-B_Cu.gbl, bogie-B_Mask.gbs, bogie-B_Paste.gbp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]
2024-01-26 Created BOM, ordered all PCBs
    [bogie.csv, bom_combined.ods, hand.csv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]
2024-01-26 All non-OV components ordered. Next up: Get OV components, ready arm for HW installation
    [bom_combined.ods, mouser_order_31289313.xls]
2024-02-07 Nothing particular, preparing for assembly
    [bom_combined.ods]
2024-03-12 Got the CAN backbone structure up and running. Need to read more about interrupts, and look at Byggern
2024-03-15 string parsing and motor control works, committing as a savepoint
2024-03-16 String commands and motor control works, tested on torso. Next up: Implement structs for other motors
2024-03-16 local control functional on all motors. Next up: CAN
2024-03-17 Notes before making ready for accelerometer integration
2024-03-22 Committing for safe state. Next up: fix accelerometer can messages
    [accelerometer_driver.c, can.c, can_driver.c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]
2024-03-23 safe state, accelerometer over CAN appears to work. Next up: move CAN cmd handlers to a separate file.
2024-03-23 moved CAN handler sto separate functions, but not separate files due to cyclical include problem
    [can_driver.c]
2024-03-23 reimplemented joint control for all joints, works! Next up: calibrate 0 for shoulder using acc
2024-03-23 Added a new struct for handling incoming accelerometer data, with getters and setters
2024-03-24 Got accelerometer data back, new CAN messaging system seems to work well.
2024-03-25 Starting ADC driver config. Still need to incorporate acc into control loop
2024-03-25 ADC with watchdog interrupt working. Next up: integrate acc, clean up and comment
2024-03-26 Accelerometer integrated into shoulder, committing before comments
2024-03-26 Added more doc, stuck on joint controller
    [accelerometer_driver.c, adc_driver.c, joint_controller.c]
2024-03-30 Documentation complete. Next up: PID and calibration
2024-03-31 Refactored motor driver to use list of motors
2024-03-31 PID complete. Next: calibration
2024-03-31 started on home calibration
2024-04-01 calibration works for individual joints. Next up: all 6 together
2024-04-03 Calibration complete
2024-04-09 PIDs are tuned acceptably well, calibration works ish. Preparing for ROS
2024-04-13 Added ROS nodes, urdf, got started on a UART parser for ROS
    [joint_limits.yaml, orca_description.urdf, ros2_controllers.yaml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]
2024-04-13 got ros integration, shoulder and rail smooth. Next up: add CAN msgs to transfer joint setpoints
2024-04-16 All joints except pinch controllable. Committing before running setup assistant
2024-04-17 various ROS improvements. Next up: PID tuning at varying voltages
    [joint_limits.yaml, orca_description.urdf, ros2_controllers.yaml]
2024-04-18 pids are tuned, overall works better. Possibly reconsider elbow int action
    [orca_description.urdf]
2024-05-01 minor code changes after testing at OV. IMPORTANT: IMU deactivated, shoulder limit to 1.5
    [orca_description.urdf]
2024-05-02 Added various diagrams, discovered that I did not merge the PCB folders with after the 1.1 updates
2024-05-02 merged pcbs from improvement phase
    [bogie.kicad_pcb, bogie.kicad_sch, hand_B.kicad_pcb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]
2024-05-07 Added pcb pdfs
    [IMU_assy.kicad_sch, can_assy.kicad_sch, hand.kicad_sch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]
2024-05-20 Minor changes to documentation, added diagrams
    [stm_config_official.txt]
2024-05-20 Found a minor bug in the voltage cap check, always used motor2 as reference. Likely no harm done. Added diagrams
    [motor_driver.c]
2024-05-25 Changed CAN handler motorSp to jointSp
2024-06-08 merged changes from timertests, mostly documentation and such. Did not add tim6 config
    [bogie.kicad_sch, can_assy.kicad_sch, hand.kicad_sch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]
2024-06-08 finalised before censure curation
    [stm_config_official.txt]
2024-09-26 got the pincer working by setting the joint type to non-gripper
    [ros2_controllers.yaml]
2024-09-27 Updated control message and control listener nodes to receive pincer value. Halved, as moveit treats the gripper teeth as two joints.
2025-08-07 selective mrg from task brnch, updates rviz config and comms layer to support pinch
    [orca_description.urdf]

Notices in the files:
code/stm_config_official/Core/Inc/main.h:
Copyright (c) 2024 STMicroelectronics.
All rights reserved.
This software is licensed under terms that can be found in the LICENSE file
